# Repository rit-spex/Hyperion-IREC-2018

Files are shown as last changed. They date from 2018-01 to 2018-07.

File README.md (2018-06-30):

# IREC-Hyperion

###### Overview
Every year Spaceport America host the Intercollegiate Rocket and Engineering Competition or IREC. Teams for colleges from across the country meet to compete in these events. The 2018 SA Cup will be held June 19-23, 2018, with events held in Las Cruces, NM. RIT SPEX will be partnering with RIT Launch Initiative to deliver our first entry into the competition. Launch Initiative will build the rocket, SPEX will provide the payload. Our goal is to design and build a scientific payload to compete in the intercollegiate rocket engineering competition.

###### Repository Contents

* ***/hardware*** - Hardware design documents
* ***/IREC-Hyperion Documentation*** - Documentation files regarding the Hyperion project
* ***/IREC-Hyperion Drop Test*** - Files regarding drop tests
* ***/IREC-Hyperion HABnet Data Feeder*** - Ground station software which collects data transmitted from payload
* ***/IREC-Hyperion Protocol*** - The Hyperion protocol software library
* ***/IREC-Hyperion System*** - System source files and libraries for the Hyperion payload
* ***/IREC-Hyperion Tests*** - Hyperion test resources 

###### Mission Patch
Hyperion Mission Patch

###### Hardware Modules
- Teensy 3.6
- Sparkfun LIS331
- Sparkfun LSM9DS1
- Adafruit BME280
- Sparkfun CCS811
- RFM_9X LoRa
- PerfectFlite StratoLogger CF

###### Contributors

Daniel Mitchell

Alec Herbert

Thomas James Hall

Dylan R. Wagner

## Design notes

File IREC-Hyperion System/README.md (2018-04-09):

# IREC-Hyperion System

###### Summary 
This sub-directory contains libraries, source files and tests pertaining to the Hyperion System Software. The system software uses a handfull of Arduino libraries as-well as custom libraries. All source files are written in C/C++ with some test files written in The Arduino programming language (.ino). 

######  Contents
* ***/lib*** - Collection of Libraries used within the system
* ***/src*** - Source files for the Hyperion system
* ***/test*** - Collection of tests

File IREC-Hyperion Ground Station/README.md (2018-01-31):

# IREC-Hyperion HABnet Data Feeder
...

## Data Processor
Software running on ground base server.

...

### Dependencies 

## System Forwarder
Software running on Arduino micro controller.

...

### Dependencies

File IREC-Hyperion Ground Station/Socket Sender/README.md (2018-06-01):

## Hyperion Socket Sender
### Reads incoming data from a serial device (see:[System Forwarder](../System%20Forwarder)) and sends it to a [HABnet](https://github.com/RIT-Space-Exploration/HABnet) instance

--- 

**Requirements:**

* socketIO-client  ([github](https://github.com/invisibleroads/socketIO-client))

        pip install socketIO-client

* pyserial ([github](https://github.com/pyserial/pyserial))

        pip install pyserial

---

**Optional Arguments:**

* `-h`, `--help`

  show help message and exit

* `-D`, `--details`

  Display various details and close

* `-H [HOSTNAME]`, `--host [HOSTNAME]`

  HABnet instance hostname

  default: `127.0.0.1`

* `-P [PORT]`, `--port [PORT]`

  HABnet instance port

  default: `3000`

* `-S [SERIAL_IN]`, `--serial [SERIAL_IN]`

  Serial input port

  default: `COM3`

* `-N` [NAME], `--name [NAME]`

  HABnet socket name

  default: `testSocket`

---

**Examples:**

    python socketsender.py 
    python socketsender.py --host 127.0.0.1 --port 3000

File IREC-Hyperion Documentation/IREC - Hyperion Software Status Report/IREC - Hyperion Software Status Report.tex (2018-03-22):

\title{IREC - Hyperion Software Status Report}
\author{
	Dylan Wagner (drw6528@rit.edu) \\
	RIT Space Exploration
}

\date{\today}

\documentclass[11pt]{article}
\usepackage{hyperref} 
\hypersetup{
    colorlinks=true,
    linkcolor=blue,
    filecolor=magenta,      
    urlcolor=cyan,
}
\urlstyle{same}

\begin{document}
\maketitle

\section{Work Completed}
This section will outline work completed on the system software of the Hyperion payload. 
\begin{itemize}
  \item Inital testing of hardware modules:
  \begin{itemize}
  	\item LSM9DS1 (Accelerometer , Gyroscope, Magnetometer) Sensor
	\item BME280 (Pressure, Humidity, Temperature) Sensor
	\item CCS811 (TVOC, CO2) Sensor
	\item LIS331 (Accelerometer) Sensor
	\item RFM\_9X LoRa 
  \end{itemize}
  \item Utility functions for hardware modules
  \begin{itemize}
   	\item LSM9DS1 (Accelerometer , Gyroscope, Magnetometer) Sensor
	\item BME280 (Pressure, Humidity, Temperature) Sensor
	\item CCS811 (TVOC, CO2) Sensor
	\item LIS331 (Accelerometer) Sensor
	\item RFM\_9X LoRa 
  \end{itemize}
  \item Defining a communication protocol for the Hyperion Payload
  \item Implementing the payload communication protocol
  \item Creation of a robust execution scheduling queue (\href{https://github.com/RIT-Space-Exploration/Dynamic-Scheduling-Queue}{Dynamic Scheduling Queue})
  \item Forked RadioHead library to work with Teensy3.6
  \item Tested:
  \begin{itemize}
  	\item Communication between RFM\_9X modules 
	\item Communication between RFM\_9X modules using the Hyperion payload Protocol
	\item The Dynamic Scheduling Queue
	\item Communication routines within the the system
  \end{itemize}	
\end{itemize}

\section{In Progress / ToDo}
This section will outline work that is in progress or will be in the near future. 
\begin{itemize}
	\item Further defining routines within the system
	\item Implementation of routines regarding:
	\begin{itemize}
		\item Gathering data from sensors, logging it
		\item Transmission of data groups with the Hyperion Protocol
		\item Writing the data buffer to the storage card
		\item Mission Events (Parachute deployment, Impact damper deployment)
		\item Maintaining impact damper pressure
	\end{itemize}
	\item Testing implemented routines
	\item Initial testing of the Pressure Transducer 
	\item Utility functions for the Pressure Transducer 
	\item Further optimizing the Hyperion Protocol for low-bandwidth environments
	\item Testing deployment sensing mechanism 
	\item Testing software with mission event tests (Parachute deployment, Impact damper deployment)
	\item Readjustment of static priority values within the Dynamic Scheduling Queue.
	\item Testing of overall system
	\item Data feeder software for ground station:
	\begin{itemize}
		\item Software to collect transmissions from payload on a micro-controller 
		\item Software to collect data over serial from connected micro-controller and feed data to HabNet
	\end{itemize}
\end{itemize}

\section{Links}
\begin{itemize}
	\item The Rochester Institute of Technology Space Exploration Website
	\\ \url{http://spex.rit.edu}
	\item The Rochester Institute of Technology Space Exploration GitHub Page \url{https://github.com/RIT-Space-Exploration}
	\item IREC - Hyperion Main Repository (GitHub)
	\\ \url{https://github.com/RIT-Space-Exploration/IREC-Hyperion}
	\item Dynamic Scheduling Queue (GitHub)
	\\ \url{https://github.com/RIT-Space-Exploration/Dynamic-Scheduling-Queue}
	\item Forked RadioHead Library (GitHub)
	\\ \url{https://github.com/RIT-Space-Exploration/RadioHead}
\end{itemize}

\end{document}

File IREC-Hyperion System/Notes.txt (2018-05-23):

Notes
04/24/18
    Data Transmission Has been axed for the test launch.
        SPI bus conflict causes race condition which eventually causes LoRa module to hang.
05/17/18
    Move LIS331 and LSM9DS1 back to SPI0 - Done
05/20/18
    Implement routine which runs in safe phase and reports health of hardware.
        - Deployment Pins
        - EMatches 
        - SD card
        - Pressure system
        - Servo
        ...

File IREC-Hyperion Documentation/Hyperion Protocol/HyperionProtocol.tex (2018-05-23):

\documentclass{article}

\usepackage[table,xcdraw]{xcolor}
\usepackage{float}
\usepackage{fancyhdr}
\pagestyle{fancy}

\title{RIT SPEX Hyperion Protocol}
\date{February 1, 2018}
\author{Dylan R. Wagner, Alec Herbert, Chris Johnson}

\begin{document}
  \pagenumbering{gobble}
  \maketitle
  \pagenumbering{arabic}
  
  \section{Abstract}
  The Hyperion Protocol defines data packing techniques and configurations in order to achieve communication between endpoints. A universal header will be defined which allows senders the freedom to include a wide range of information from individual sensors or information groups. In addition, multiple other data configurations will be defined. These additional data configurations will store information regarding data groups from sensors without any notion of time captured.
  
  \section{Header}
  The header will be required for any outgoing and incoming data within the realm of the Hyperion protocol. This header will include information regarding the which data group (Sensor values) is contained in a message, flags and time sent. Any data wished to be sent with the Hyperion Protocol will be tacked on behind the header.  The Hyperion Protocol header will be \textbf{24bits} long or \textbf{3 bytes}.
  \subsection{Header Data}
  Data contained in the header will have a maximum size, this size will be defined in bits and largest value stored. 
  
  \paragraph{Data Group (4 bits)}
  The Data Group section will contain information to distinguish which data is contained after the header. A size of 4 bits will be allocated to this section, this allows for 16 separate values. This will be plenty for the number of data groups sent within the Hyperion system. 
  
  \paragraph{Flags (4 bits)}
  The Flags section will be used to define how the data will be parsed or handled. A size of 4 bits will allow for 4 flags to be set at a time.
  
  \paragraph{Sent Time (16 bits)}
  The Sent Time section will be used to determine the time sent in seconds from the Hyperion system. This will be used for timestamps/data evolution analysis. This section will need to be 16 bits. This allows for a value of maximum value of 65535. This allows us to send data time stamped from startup for 18.2 hours. 
  
  \subsection{Visualization}
  
  \begin{table}[h]
  \centering
  \caption{Hyperion Header}
  \label{Hyperion Header}
  \begin{tabular}{|c|c|c|l|l|l|l|l|l|l|lll}
  \cline{1-10}
  1 & 2 & \multicolumn{8}{c|}{Sent Time (16 bits)} &  & 1 & Data Group (4 bits) \\ \cline{1-10}
  \multicolumn{10}{|c|}{Data}                      &  & 2 & Flags (4 bits)      \\ \cline{1-10}
  \end{tabular}
  \end{table}
  
  \subsection{Header Values}
  This section displays mappings between header values and their meanings. In the header only two sections will need further definitions. These sections are the Data Group and Flags sections.
  
  \subsubsection{Data Group Mapping}
  
  \begin{table}[h]
  \centering
  \caption{Data Group Mapping}
  \begin{tabular}{ll}
  Value & Mapping \\
  0     & No Data \\
  1     & LSM9DS1     \\
  2     & BME280        \\
  3     & CCS811        \\
  4     & LIS331      \\
  5     & PerfectFlite Strato Logger       \\
  6     & Orientation   \\
  7     &  Commands  \\
  8     &         \\
  9     &         \\
  10    &         \\
  11    &         \\
  12    &         \\
  13    &         \\
  14    &         \\
  15    &        
  \end{tabular}
  \end{table}
  
  \pagebreak
  
  \section{Data Groups}
  \subsection{LSM9DS1}
  This section will define the data frame for the LSM9DS1 data group. The LSM9DS1 data group contains information regarding acceleration, gyroscope and magnetometer sensors in the X, Y and Z axis. In total, this data frame will be 36 bytes in size. 
  \subsubsection{LSM9DS1 Data}
  \paragraph{Acceleration X, Y, Z (12 bytes - 96 bits)}
  The acceleration section of the LSM9DS1 data frame will store the X, Y, Z values. Each axis is 4 bytes or 32 bits long. The X, Y, Z values will be placed in that order.
  \paragraph{Gyroscope X, Y, Z (12 bytes - 96 bits)}
  The gyroscope section of the LSM9DS1 data frame will store the X, Y, Z values. Each axis is 4 bytes or 32 bits long. The X, Y, Z values will be placed in that order.
  \paragraph{Magnetometer X, Y, Z (12 bytes - 96 bits)}
  The magnetometer section of the LSM9DS1 data frame will store the X, Y, Z values. Each axis is 4 bytes or 32 bits long. The X, Y, Z values will be placed in that order.
  \subsubsection{Visualization}
  
  \begin{table}[h]
  \centering
  \caption{LSM9DS1 Data frame}
  \begin{tabular}{|l|l|l|l|l|l|l|l|l|l|l|l|}
  \hline
  \multicolumn{4}{|l|}{ax (4 bytes)} & \multicolumn{4}{l|}{ay (4 bytes)} & \multicolumn{4}{l|}{az (4 bytes)} \\ \hline
  \multicolumn{4}{|l|}{gx (4 bytes)} & \multicolumn{4}{l|}{gy (4 bytes)} & \multicolumn{4}{l|}{gz (4 bytes)} \\ \hline
  \multicolumn{4}{|l|}{mx (4 bytes)} & \multicolumn{4}{l|}{my (4 bytes)} & \multicolumn{4}{l|}{mz (4 bytes)} \\ \hline
  \end{tabular}
  \end{table}

  \pagebreak

  \subsection{BME280}
  This section will define the data frame for the BME280 data group. The BME280 data group contains information regarding atmospheric temperature, pressure and humidity. In total, this data frame will be 8 bytes in size.
  \subsubsection{BME280 Data}
  \paragraph{Temperature (2 bytes)}
  The temperature section of the BME280 data frame will store the atmospheric temperature in degrees Celsius. In total, the temperature section will be 2 bytes.
  \paragraph{Pressure (2 bytes)}
  The pressure section of the BME280 data frame will store the atmospheric pressure in kPa. In total, the pressure section will be 2 bytes.
  \paragraph{Humidity (2 bytes)}
  The humidity section of the BME280 data frame will store the atmospheric humidity by percentage. In total, the humidity section will be 4 bytes.
  \paragraph{BME\_Altitude (2 bytes)}
  The Altitude section of the BME280 data frame will store the altitude derived by pressure. In total, the BME\_Altitude section will be 2 bytes.
  \subsubsection{Visualization}
  
  \begin{table}[H]
  \centering
  \caption{BME280 Data Group}
  \label{my-label}
  \begin{tabular}{|l|l|}
  \hline
Temperature (2 bytes) & Pressure (2 bytes)      \\ \hline
Humidity (2 bytes)    & BME\_Altitude (2 bytes) \\ \hline
  \end{tabular}
  \end{table}
  
  \pagebreak
  
  \subsection{CCS811}
  This section will define the data frame for the the CCS811 data group. The CCS811 data group contains information regarding atmospheric composition. In,      total, this data frame will be 4 bytes in size.
  \subsubsection{CCS811 Data}
  \paragraph{Total Volatile Organic Compounds (2 Bytes)}
  The Total Volatile Organic Compounds section of the CCS811 data frame will store the total volatile organic compounds in ppm. In total, this section will be 2 bytes.
  \paragraph{Equivalent Carbon Dioxide (2 Bytes)}
  The Equivalent Carbon Dioxide section of the CCS811 data frame will store the equivalent carbon dioxide in ppm. In total, this section will be 2 bytes in size.
  \subsubsection{Visualization}
  
  \begin{table}[H]
  \centering
  \caption{CCS811 Data Frame}
  \label{my-label}
  \begin{tabular}{|l|l|}
  \hline
VOC (2 bytes) & ECD (2 bytes) \\ \hline 
  \end{tabular}
  \end{table}
 
  \pagebreak
 
 \subsection{LIS331}
 This section will define the data frame for the the LIS331 data group. The LIS331 data group contains information acceleration in Gees. In,  total, this data frame will be 12 bytes in size.
 \subsubsection{LIS331 Data}
 \paragraph{X, Y, Z Acceleration (12 bytes)}
 The Acceleration section of the LIS331 data frame will store the acceleration sensor readings in Gees. The X, Y, Z parts of this section will be 4 bytes each. In total, this data section will be 12 bytes.
 \subsubsection{Visualization}
 
 \begin{table}[H]
 \centering
 \caption{LIS331 Data Frame}
 \label{my-label}
 \begin{tabular}{|l|l|l|}
 \hline
Acceleration (X) & Acceleration (Y) & Acceleration (Z) \\ \hline
 \end{tabular}
 \end{table}
 
 \pagebreak
 
  \subsection{PerfectFlite Strato Logger}
  This section will define the data frame for the Strato Logger data group. The Strato Logger data group provides accurate information regarding altitude. In total, this data group will be 4 bytes in size.
  \subsubsection{Strato Logger Data}
  \paragraph{Altitude (4 bytes)}
  The Altitude section of the Strato Logger data group will store the altitude in meters. In total, this data section will be 4 bytes in size.
  
  \subsubsection{Visualization}
  \begin{table}[H]
  \centering
  \caption{PerfectFlite Strato Logger Data Group}
  \label{my-label}
  \begin{tabular}{|l|}
  \hline
Altitude (2 bytes) \\ \hline
 \end{tabular}
 \end{table}
  
 \pagebreak
  
  \subsection{Orientation}
  
  This section will define the data frame for the Orientation data group. The Orientation data group will contain calculations for Roll, Pitch and Yaw. In total, this data group will be 4 bytes in size. Values will be 9 bits in length with the signed bits being stored within the first byte. 
  \subsubsection{Orientation Data}
  \paragraph{Roll (9 bits)}
  The Roll section of the Orientation data group will store the Roll from range -180 to 180 (0 to 360 degrees).
  \paragraph{Pitch (9 bits)}
  The Pitch section of the Orientation data group will store the Pitch from range -90 to 90 (0 to 180 degrees).  
  \paragraph{Yaw (9 bits)}
  The Yaw section of the Orientation data group will store the Yaw from range -180 to 180 (0 to 360 degrees).  
  
  \subsubsection{Visualization}
  \begin{table}[H]
  \centering
  \caption{Orientation Data Group}
  \label{Orientation}
  \begin{tabular}{|l|l|l|l|}
  \hline
  
Signed(1 byte) & Roll(1 byte) & Pitch(1 byte) & Yaw(1 byte) \\ \hline

  \end{tabular}
  \end{table}
  
 \pagebreak  
  
  \subsection{Commands/Command Info}
  This section will outline the header configurations for separate commands to and from the payload. This Group will hold no data, thus this data frame is 0 bytes in size. Header flags will be used in place of a data frame.
  \subsubsection{Flags}

  \begin{table}[h]
  \centering
  \caption{Flag Meanings}
  \begin{tabular}{ll}
    Bit Pos(Most significant) & Meaning \\
  0     & Arm Payload \\
  1     & Disarm Payload     \\
  2     & Payload Armed        \\
  3     & Payload Disarmed       \\
  \end{tabular}
  \end{table}
  
  \pagebreak
  
  \subsection{Info Messages}
  This section will outline the anatomy of a info message data frame. This data frame has no defined length, only a length of greater than 3 bytes.
  
  \subsubsection{Data}
  Data attached to this frame will be stored in the form of a string. This string has no defined length. However it will be less than the maximum length of transmitted packets defined by the communication device.
   
  \lfoot{Latest Revision: \today}

  \end{document}

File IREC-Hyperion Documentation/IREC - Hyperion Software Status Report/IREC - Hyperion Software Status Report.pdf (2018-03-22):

## IREC - Hyperion Software Status Report

Dylan Wagner (drw6528@rit.edu) RIT Space Exploration

March 22, 2018

## 1 Work Completed

This section will outline work completed on the system software of the Hyperion payload.

- Inital testing of hardware modules:

– LSM9DS1 (Accelerometer , Gyroscope, Magnetometer) Sensor

– BME280 (Pressure, Humidity, Temperature) Sensor

– CCS811 (TVOC, CO2) Sensor

– LIS331 (Accelerometer) Sensor

– RFM 9X LoRa

- Utility functions for hardware modules

– LSM9DS1 (Accelerometer , Gyroscope, Magnetometer) Sensor

– BME280 (Pressure, Humidity, Temperature) Sensor

– CCS811 (TVOC, CO2) Sensor

– LIS331 (Accelerometer) Sensor

– RFM 9X LoRa

- Defining a communication protocol for the Hyperion Payload
- Implementing the payload communication protocol
- Creation of a robust execution scheduling queue (Dynamic Scheduling Queue) (https://github.com/RIT-Space-Exploration/Dynamic-Scheduling-Queue)
- Forked RadioHead library to work with Teensy3.6

1

- Tested:

– Communication between RFM 9X modules

– Communication between RFM 9X modules using the Hyperion payload Protocol

– The Dynamic Scheduling Queue

– Communication routines within the the system

## 2 In Progress / ToDo

This section will outline work that is in progress or will be in the near future.

- Further defining routines within the system
- Implementation of routines regarding:

– Gathering data from sensors, logging it

– Transmission of data groups with the Hyperion Protocol

– Writing the data buffer to the storage card

– Mission Events (Parachute deployment, Impact damper deployment)

– Maintaining impact damper pressure

- Testing implemented routines
- Initial testing of the Pressure Transducer
- Utility functions for the Pressure Transducer
- Further optimizing the Hyperion Protocol for low-bandwidth environments
- Testing deployment sensing mechanism
- Testing software with mission event tests (Parachute deployment, Impact damper deployment)
- Readjustment of static priority values within the Dynamic Scheduling Queue.
- Testing of overall system

2

- Data feeder software for ground station:

– Software to collect transmissions from payload on a micro-controller

– Software to collect data over serial from connected micro-controller and feed data to HabNet

## 3 Links

- The Rochester Institute of Technology Space Exploration Website http://spex.rit.edu
- The Rochester Institute of Technology Space Exploration GitHub Page https://github.com/RIT-Space-Exploration
- IREC - Hyperion Main Repository (GitHub) https://github.com/RIT-Space-Exploration/IREC-Hyperion
- Dynamic Scheduling Queue (GitHub) https://github.com/RIT-Space-Exploration/Dynamic-Scheduling-Queue
- Forked RadioHead Library (GitHub) https://github.com/RIT-Space-Exploration/RadioHead

3

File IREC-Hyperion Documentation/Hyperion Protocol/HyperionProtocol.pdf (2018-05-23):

# RIT SPEX Hyperion Protocol

Dylan R. Wagner, Alec Herbert, Chris Johnson

February 1, 2018

## 1 Abstract

The Hyperion Protocol defines data packing techniques and configurations in order to achieve communication between endpoints. A universal header will be defined which allows senders the freedom to include a wide range of information from individual sensors or information groups. In addition, multiple other data configurations will be defined. These additional data configurations will store information regarding data groups from sensors without any notion of time captured.

## 2 Header

The header will be required for any outgoing and incoming data within the realm of the Hyperion protocol. This header will include information regarding the which data group (Sensor values) is contained in a message, flags and time sent. Any data wished to be sent with the Hyperion Protocol will be tacked on behind the header. The Hyperion Protocol header will be 24bits long or 3 bytes.

### 2.1 Header Data

Data contained in the header will have a maximum size, this size will be defined in bits and largest value stored.

Data Group (4 bits) The Data Group section will contain information to distinguish which data is contained after the header. A size of 4 bits will be allocated to this section, this allows for 16 separate values. This will be plenty for the number of data groups sent within the Hyperion system.

Flags (4 bits) The Flags section will be used to define how the data will be parsed or handled. A size of 4 bits will allow for 4 flags to be set at a time.

1

2.2 Visualization | 2 HEADER

Sent Time (16 bits) The Sent Time section will be used to determine the time sent in seconds from the Hyperion system. This will be used for times-tamps/data evolution analysis. This section will need to be 16 bits. This allows for a value of maximum value of 65535. This allows us to send data time stamped from startup for 18.2 hours.

### 2.2 Visualization

Table 1: Hyperion Header
1 | 2 | Sent Time (16 bits) | 1 | Data Group (4 bits)
| | Data | 2 | Flags (4 bits)

### 2.3 Header Values

This section displays mappings between header values and their meanings. In the header only two sections will need further definitions. These sections are the Data Group and Flags sections.

### 2.3.1 Data Group Mapping

Table 2: Data Group Mapping
Value | Mapping
0 | No Data
1 | LSM9DS1
2 | BME280
3 | CCS811
4 | LIS331
5 | PerfectFlite Strato Logger
6 | Orientation
7 | Commands
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
3 DATA GROUPS

## 3 Data Groups

### 3.1 LSM9DS1

This section will define the data frame for the LSM9DS1 data group. The LSM9DS1 data group contains information regarding acceleration, gyroscope and magnetometer sensors in the X, Y and Z axis. In total, this data frame will be 36 bytes in size.

### 3.1.1 LSM9DS1 Data

Acceleration X, Y, Z (12 bytes - 96 bits) The acceleration section of the LSM9DS1 data frame will store the X, Y, Z values. Each axis is 4 bytes or 32 bits long. The X, Y, Z values will be placed in that order.

Gyroscope X, Y, Z (12 bytes - 96 bits) The gyroscope section of the LSM9DS1 data frame will store the X, Y, Z values. Each axis is 4 bytes or 32 bits long. The X, Y, Z values will be placed in that order.

Magnetometer X, Y, Z (12 bytes - 96 bits) The magnetometer section of the LSM9DS1 data frame will store the X, Y, Z values. Each axis is 4 bytes or 32 bits long. The X, Y, Z values will be placed in that order.

### 3.1.2 Visualization

Table 3: LSM9DS1 Data frame
ax (4 bytes) | ay (4 bytes) | az (4 bytes)
gx (4 bytes) | gy (4 bytes) | gz (4 bytes)
mx (4 bytes) | my (4 bytes) | mz (4 bytes)

3

3.2 BME280 | 3 DATA GROUPS

### 3.2 BME280

This section will define the data frame for the BME280 data group. The BME280 data group contains information regarding atmospheric temperature, pressure and humidity. In total, this data frame will be 8 bytes in size.

### 3.2.1 BME280 Data

Temperature (2 bytes) The temperature section of the BME280 data frame will store the atmospheric temperature in degrees Celsius. In total, the temperature section will be 2 bytes.

Pressure (2 bytes) The pressure section of the BME280 data frame will store the atmospheric pressure in kPa. In total, the pressure section will be 2 bytes.

Humidity (2 bytes) The humidity section of the BME280 data frame will store the atmospheric humidity by percentage. In total, the humidity section will be 4 bytes.

BME Altitude (2 bytes) The Altitude section of the BME280 data frame will store the altitude derived by pressure. In total, the BME Altitude section will be 2 bytes.

### 3.2.2 Visualization

Table 4: BME280 Data Group
Temperature (2 bytes) | Pressure (2 bytes)
Humidity (2 bytes) | BME Altitude (2 bytes)

4

3.3 CCS811 | 3 DATA GROUPS

### 3.3 CCS811

This section will define the data frame for the the CCS811 data group. The CCS811 data group contains information regarding atmospheric composition. In, total, this data frame will be 4 bytes in size.

### 3.3.1 CCS811 Data

Total Volatile Organic Compounds (2 Bytes) The Total Volatile Organic Compounds section of the CCS811 data frame will store the total volatile organic compounds in ppm. In total, this section will be 2 bytes.

Equivalent Carbon Dioxide (2 Bytes) The Equivalent Carbon Dioxide section of the CCS811 data frame will store the equivalent carbon dioxide in ppm. In total, this section will be 2 bytes in size.

### 3.3.2 Visualization

Table 5: CCS811 Data Frame VOC (2 bytes) ECD (2 bytes)

5

3.4 LIS331 | 3 DATA GROUPS

### 3.4 LIS331

This section will define the data frame for the the LIS331 data group. The LIS331 data group contains information acceleration in Gees. In, total, this data frame will be 12 bytes in size.

### 3.4.1 LIS331 Data

X, Y, Z Acceleration (12 bytes) The Acceleration section of the LIS331 data frame will store the acceleration sensor readings in Gees. The X, Y, Z parts of this section will be 4 bytes each. In total, this data section will be 12 bytes.

### 3.4.2 Visualization

Table 6: LIS331 Data Frame
Acceleration (X) | Acceleration (Y) | Acceleration (Z)

6

3.5 PerfectFlite Strato Logger | 3 DATA GROUPS

### 3.5 PerfectFlite Strato Logger

This section will define the data frame for the Strato Logger data group. The Strato Logger data group provides accurate information regarding altitude. In total, this data group will be 4 bytes in size.

### 3.5.1 Strato Logger Data

Altitude (4 bytes) The Altitude section of the Strato Logger data group will store the altitude in meters. In total, this data section will be 4 bytes in size.

### 3.5.2 Visualization

Table 7: PerfectFlite Strato Logger Data Group Altitude (2 bytes)

7

3.6 Orientation | 3 DATA GROUPS

### 3.6 Orientation

This section will define the data frame for the Orientation data group. The Orientation data group will contain calculations for Roll, Pitch and Yaw. In total, this data group will be 4 bytes in size. Values will be 9 bits in length with the signed bits being stored within the first byte.

### 3.6.1 Orientation Data

Roll (9 bits) The Roll section of the Orientation data group will store the Roll from range -180 to 180 (0 to 360 degrees).

Pitch (9 bits) The Pitch section of the Orientation data group will store the Pitch from range -90 to 90 (0 to 180 degrees).

Yaw (9 bits) The Yaw section of the Orientation data group will store the Yaw from range -180 to 180 (0 to 360 degrees).

### 3.6.2 Visualization

Table 8: Orientation Data Group
Signed(1 byte) | Roll(1 byte) | Pitch(1 byte) | Yaw(1 byte)

8

3.7 Commands/Command Info | 3 DATA GROUPS

### 3.7 Commands/Command Info

This section will outline the header configurations for separate commands to and from the payload. This Group will hold no data, thus this data frame is 0 bytes in size. Header flags will be used in place of a data frame.

### 3.7.1 Flags

Table 9: Flag Meanings
Bit Pos(Most significant) | Meaning
0 | Arm Payload
1 | Disarm Payload
2 | Payload Armed
3 | Payload Disarmed

9

3.8 Info Messages | 3 DATA GROUPS

### 3.8 Info Messages

This section will outline the anatomy of a info message data frame. This data frame has no defined length, only a length of greater than 3 bytes.

### 3.8.1 Data

Data attached to this frame will be stored in the form of a string. This string has no defined length. However it will be less than the maximum length of transmitted packets defined by the communication device.

Latest Revision: May 19, 2018 | 10

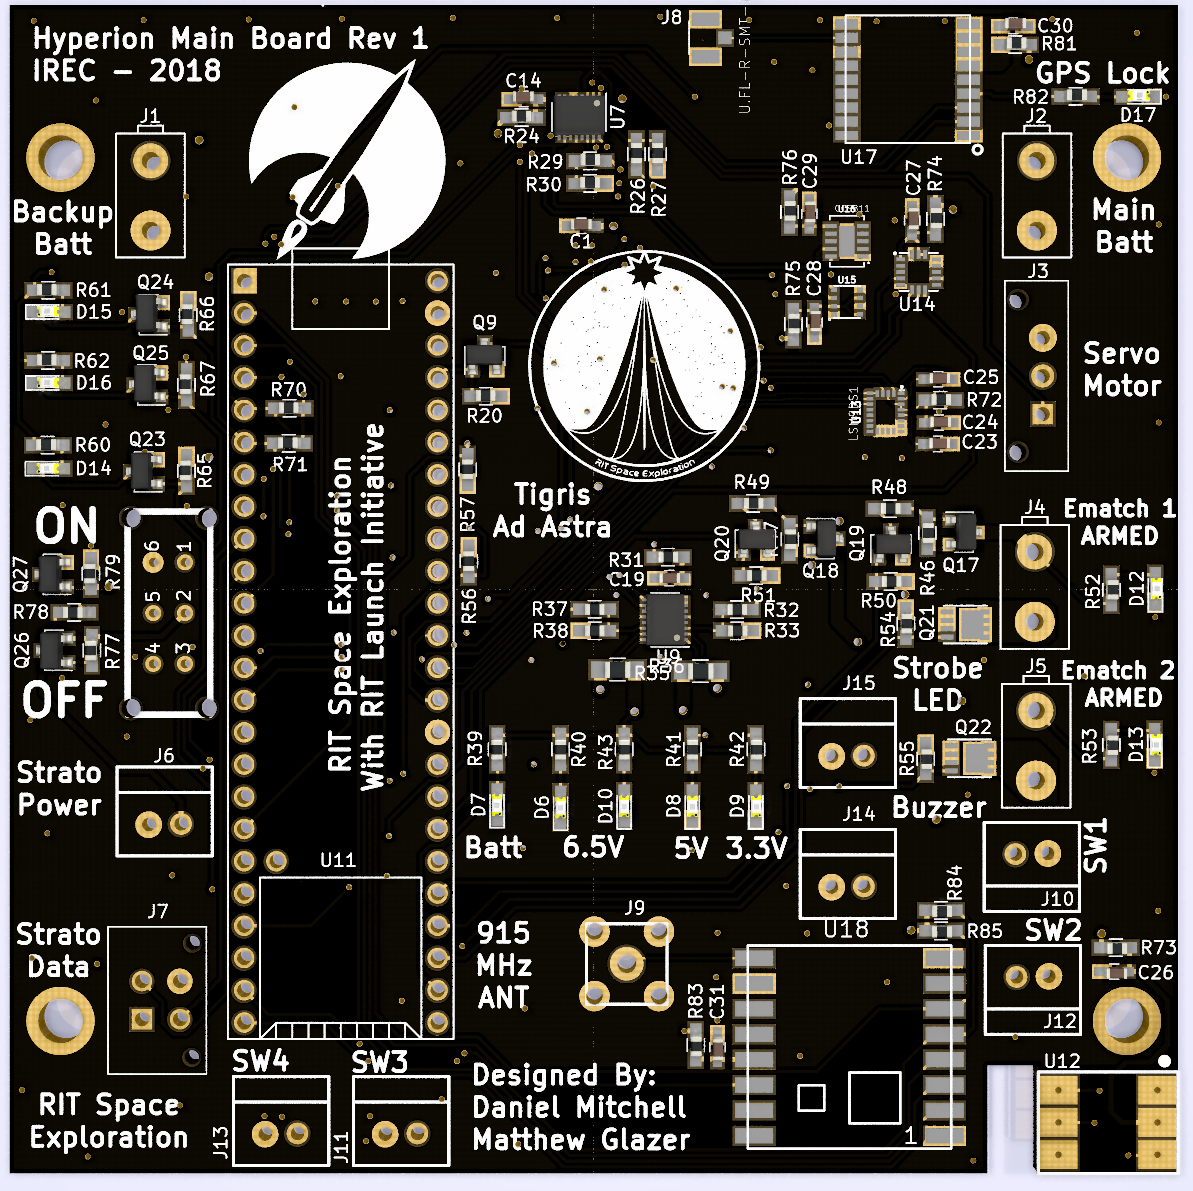
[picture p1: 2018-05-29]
Hardware/MainboardRev1/Images/Front_Rev1.PNG

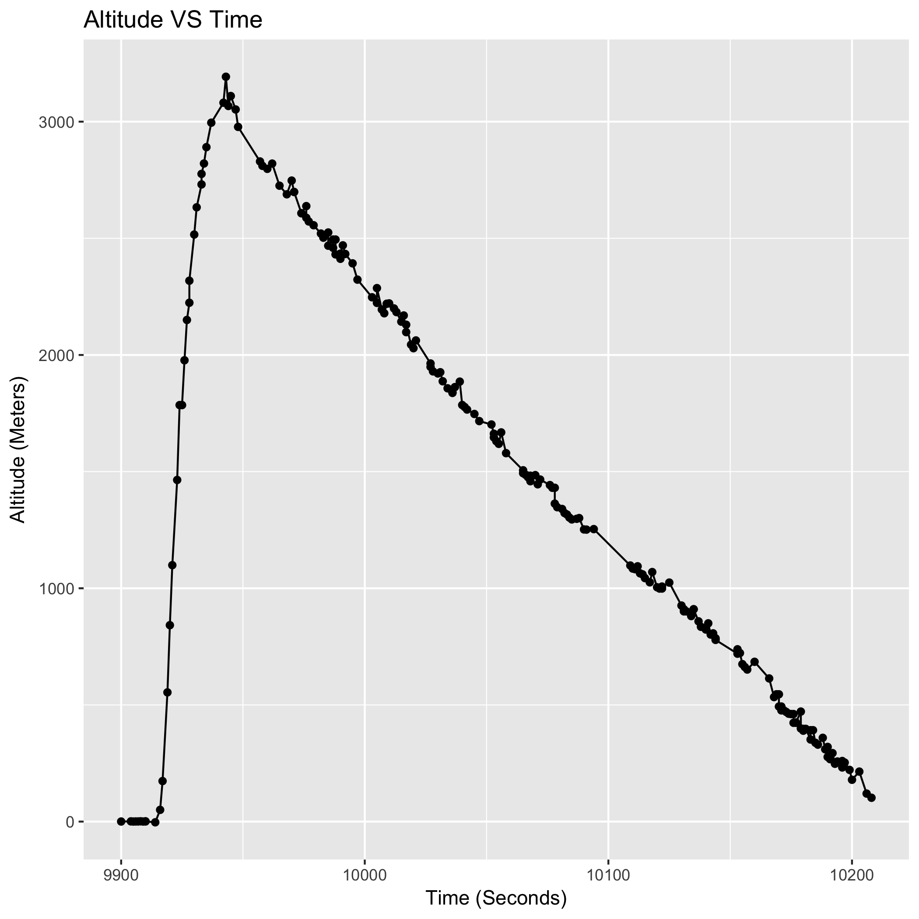
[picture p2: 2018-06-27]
IREC 2018 Flight/Scripts/alt.png

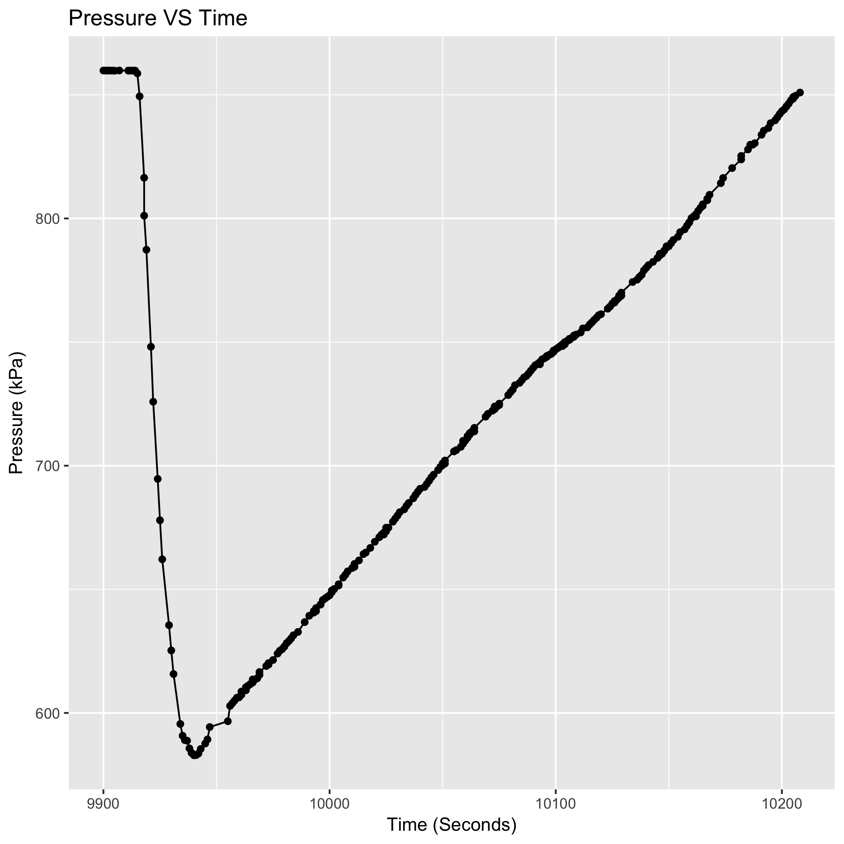
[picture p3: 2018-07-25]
IREC 2018 Flight/Scripts/Pressure.png

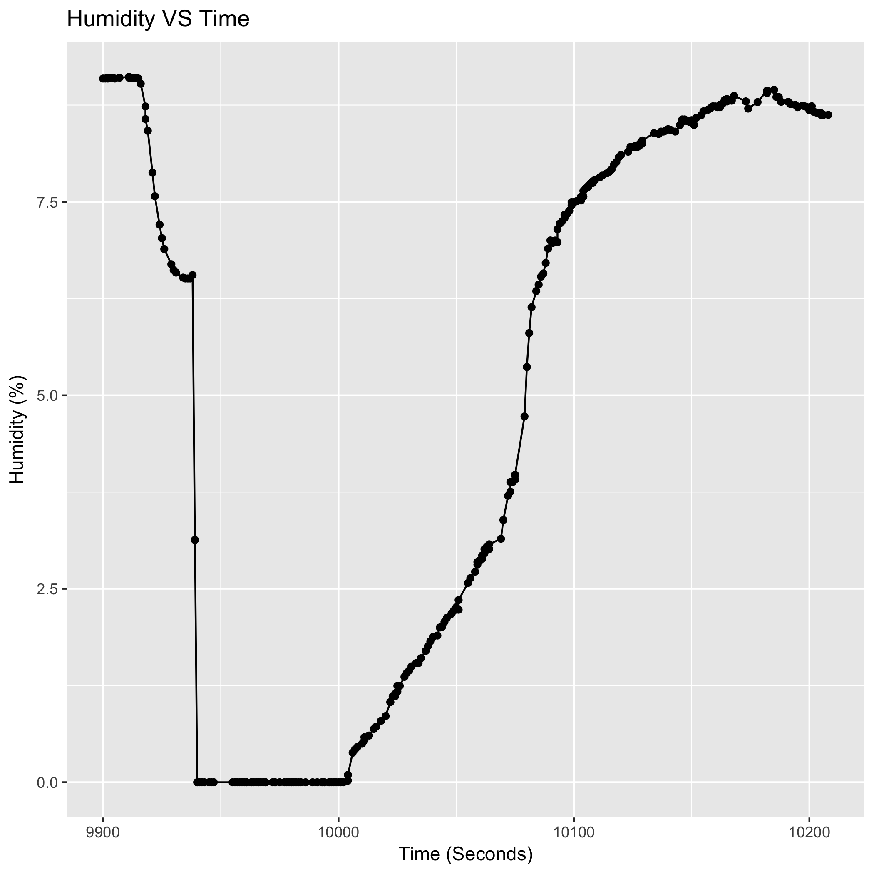
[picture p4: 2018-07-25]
IREC 2018 Flight/Scripts/Humidity.png

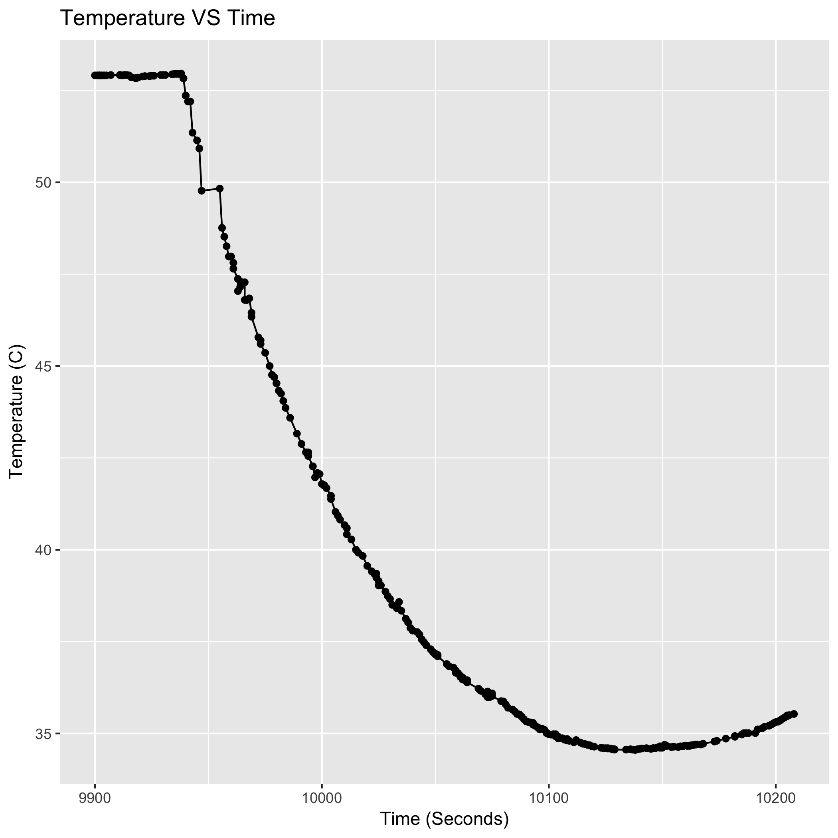
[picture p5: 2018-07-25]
IREC 2018 Flight/Scripts/Temperature.png

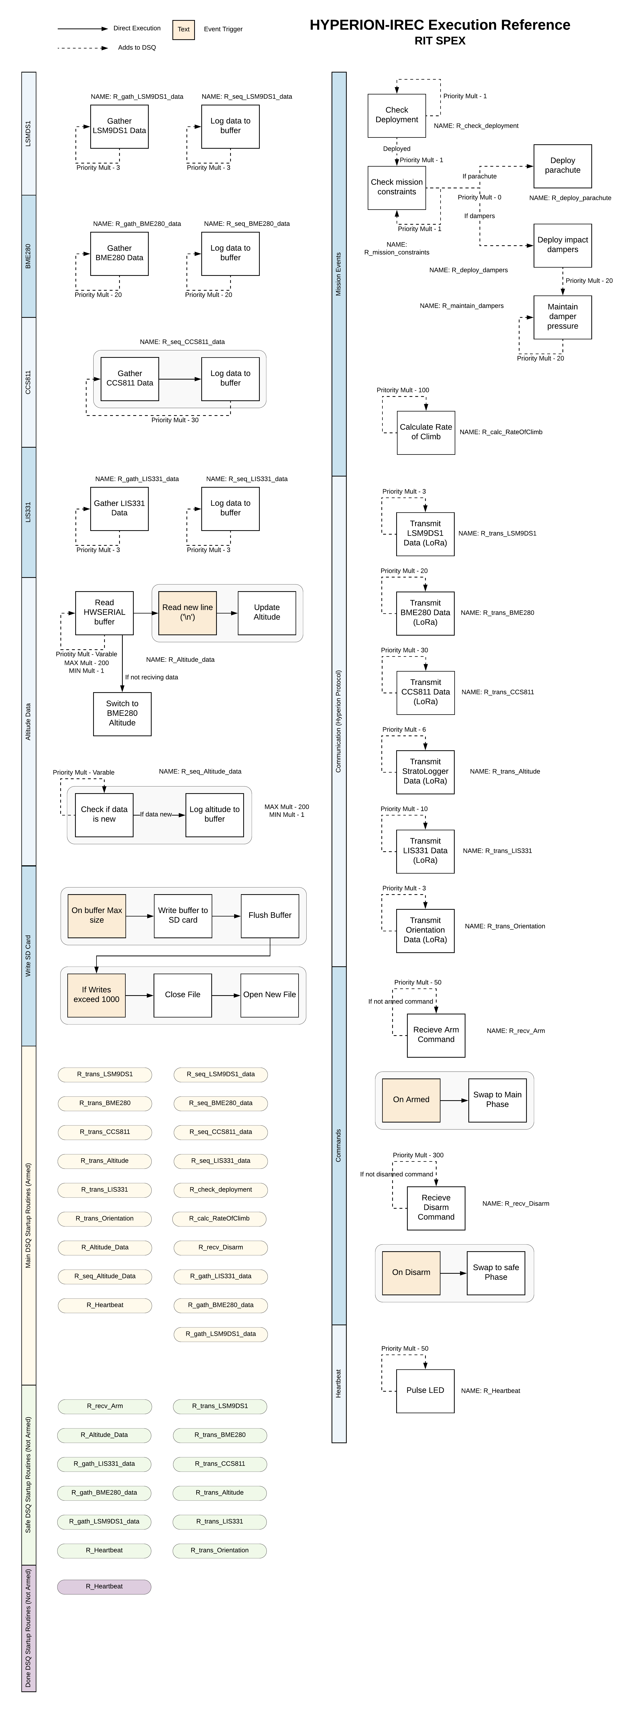
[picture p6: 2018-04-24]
IREC-Hyperion Documentation/Hyperion-IREC Execution Reference/HYPERION-IREC Execution Reference.png

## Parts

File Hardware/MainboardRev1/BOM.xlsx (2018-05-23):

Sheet: Rev 1
RIT Space Exploration - Hyperion Scientific Payload for the Intercollegiate Rocket Engineering Competition Main board Rev 1 Bill of Materials
Ref | Description | Manf Part Number | Manf | Footprint | Purchase Link | Quantity | Price | Sub Total
C4 C23 C32 C33 C34 C35 | .01uF, 100V |  |  | 0603 | Digikey (https://www.digikey.com/product-detail/en/tdk-corporation/C1608X7R2A103M080AA/445-1305-1-ND/567707)
C1 C5 C6 C14 C19 C24 C25 C26 C27 C28 C29 C30 C31 | 0.1uF, 50V |  |  | 0603 | Digikey (https://www.digikey.com/product-detail/en/samsung-electro-mechanics/CL10B104MB8NNNC/1276-1941-1-ND/3890027)
C7 | 10pF, 25V |  |  | 0603 | Digikey (https://www.digikey.com/product-detail/en/avx-corporation/06033C100KAT2A/478-11366-1-ND/8019119)
C8 | 220pF, 100V |  |  | 0603 | Digikey (https://www.digikey.com/product-detail/en/samsung-electro-mechanics/CL10B221KC8WPNC/1276-6656-1-ND/5961515)
C2 C3 C9 C10 C11 C12 C13 C15 C16 C17 C18 C20 C21 C22 | 47uF, 16V |  |  | 1210 | Digikey (https://www.digikey.com/product-detail/en/murata-electronics-north-america/GRM32ER61C476ME15K/490-8355-1-ND/4380649)
D5 | 3.3V Zener |  |  |  | Digikey (https://www.digikey.com/product-detail/en/vishay-semiconductor-diodes-division/BZX384B5V6-E3-18/BZX384B5V6-E3-18GICT-ND/8564886)
D1 D2 | 5.6V Zener |  |  |  | Digikey (https://www.digikey.com/product-detail/en/diodes-incorporated/MMSZ5232BS-7-F/MMSZ5232BS-FDICT-ND/815868)
D3 | Schottky Diode (Switching Regulator) |  |  |  | Digikey (https://www.digikey.com/product-detail/en/central-semiconductor-corp/CMDSH2-3-TR/CMDSH2-3CT-ND/4806979)
D15 D17 | Blue LED | 3.3Vf, 20mA, 104mcd |  |  | Digikey (https://www.digikey.com/product-detail/en/lite-on-inc/LTST-C194TBKT/160-1837-1-ND/2356236)
D6 D7 D8 D9 D14 | Green LED | 3.4Vf, 10mA, 98mcd |  |  | Digikey (https://www.digikey.com/product-detail/en/osram-opto-semiconductors-inc/LT-L29S-P2R1-25-Z/475-2774-1-ND/1938941)
D10 D12 D13 D16 | Red LED | 2Vf, 20mA, 104mcd |  |  | Digikey (https://www.digikey.com/product-detail/en/osram-opto-semiconductors-inc/LS-Q976-NR-1/475-2512-1-ND/1802639)
D4 D11 | Schottky Diode 20V 4A |  |  |  | Digikey (https://www.digikey.com/product-detail/en/vishay-semiconductor-diodes-division/SL42-E3-57T/SL42-E3-57TGICT-ND/1091621)
J9 |  | CONN_RP-SMA_Right_Angle_0733910320 |  |  | Digikey (https://www.digikey.com/products/en?keywords=0733910320)
J1 J2 J4 J5 |  | CONN_2POS_VERT_TE_CONN |  |  | Digikey (https://www.digikey.com/scripts/DkSearch/dksus.dll?Detail&itemSeq=261636948&uq=636626302055901696)
Mates for Above |  |  |  |  | Digikey (https://www.digikey.com/scripts/DkSearch/dksus.dll?Detail&itemSeq=261636940&uq=636626302055891695)
J6 J10 J11 J12 J13 J14 J15 |  |  |  |  | Digikey (https://www.digikey.com/scripts/DkSearch/dksus.dll?Detail&itemSeq=261713276&uq=636626432256830487)
Mates for Above |  |  |  |  | Digikey (https://www.digikey.com/scripts/DkSearch/dksus.dll?Detail&itemSeq=261713294&uq=636626432256830487)
J3 |  | Molex_Microfit3_Header_01x03_Straight |  |  | Digikey (https://www.digikey.com/product-detail/en/molex-llc/0436500315/WM1918-ND/283462)
Mates for Above |  |  |  |  | Digikey (https://www.digikey.com/product-detail/en/molex-llc/43645-0300/WM1846-ND/268975)
J7 |  | 4-Pin_Molex_Vertical |  |  | Digikey (https://www.digikey.com/product-detail/en/molex-llc/0430450427/WM10667-ND/3310189)
Mates for Above |  |  |  |  | Digikey (https://www.digikey.com/product-detail/en/molex-llc/0430250408/WM11225-ND/4481508)
J8 |  | HRS_U.FL-R-SMT-1(10) |  |  | Digikey (https://www.digikey.com/scripts/DkSearch/dksus.dll?Detail&itemSeq=261624801&uq=636626300194543747)
TE Connectivity AMP Pins |  |  |  |  | Digikey (https://www.digikey.com/scripts/DkSearch/dksus.dll?Detail&itemSeq=261705411&uq=636626302055951701)
Other TE Connectivity Pins??? |  |  |  |  | Digikey (https://www.digikey.com/scripts/DkSearch/dksus.dll?Detail&itemSeq=261713305&uq=636626432256840488)
Molex Pins |  |  |  |  | Digikey (https://www.digikey.com/product-detail/en/molex-llc/43030-0001/WM1837CT-ND/467810)
 |  |  |  |  |  | 0 |  | 0.00
L1 | 2.2uH | RLF7030T-2R2M5R4 |  |  | Digikey (https://www.digikey.com/product-detail/en/tdk-corporation/RLF7030T-2R2M5R4/445-2962-1-ND/1068729)
 |  |  |  |  |  | 0 |  | 0.00
Q5 Q6 Q7 Q9 Q11 Q12 Q13 Q14 Q16 Q19 Q20 Q23 Q24 Q25 Q27 Q30 Q31 |  | NTR4003 |  |  | Digikey (https://www.digikey.com/product-detail/en/on-semiconductor/NTR4003NT3G/NTR4003NT3GOSCT-ND/1967271)
Q21 Q22 |  | SIS612EDNT-T1-GE3 |  |  | Digikey (https://www.digikey.com/product-detail/en/vishay-siliconix/SIS612EDNT-T1-GE3/SIS612EDNT-T1-GE3CT-ND/7622753)
Q1 Q2 Q3 Q4 Q8 Q10 Q15 Q17 Q18 Q26 Q28 Q29 |  | SSM3J328R |  |  | Digikey (https://www.digikey.com/product-detail/en/toshiba-semiconductor-and-storage/SSM3J358RLF/SSM3J358RLFCT-ND/7394090)
 |  |  |  |  |  | 0 |  | 0.00
R80 | 0 | 0 |  |  | Digikey (https://www.digikey.com/product-detail/en/vishay-dale/CRCW06030000Z0EA/541-0.0GCT-ND/1179296)
R5 R24 R31 R72 R73 R74 R75 R76 R81 R83 | 10 | 10 |  |  | Digikey (https://www.digikey.com/product-detail/en/rohm-semiconductor/ESR03EZPJ100/RHM10DCT-ND/1983775)
R1 R2 R34 | 100k | 100k |  |  | Digikey (https://www.digikey.com/product-detail/en/rohm-semiconductor/ESR03EZPF1003/RHM100KADCT-ND/1983754)
R4 R6 R8 R12 R13 R16 R18 R20 R21 R23 R44 R45 R46 R47 R50 R51 R54 R55 R65 R66 R67 R70 R71 R77 R79 R84 R85 R86 R87 R90 R91 R94 R95 R98 R99 | 10k | 10k |  |  | Digikey (https://www.digikey.com/product-detail/en/vishay-dale/CRCW060310K0FKEA/541-10.0KHCT-ND/1179924)
R25 R28 | 10m | 10m |  |  | Digikey (https://www.digikey.com/product-detail/en/susumu/KRL1220E-M-R010-F-T5/408-1544-1-ND/3737726)
R59 R64 R69 | 11.3k | 11.3k |  |  | Digikey (https://www.digikey.com/product-detail/en/panasonic-electronic-components/ERJ-3EKF1132V/P11.3KHCT-ND/198121)
R27 R30 R33 R38 | 11.5k | 11.5k |  |  | Digikey (https://www.digikey.com/product-detail/en/yageo/RC0603FR-0711K5L/311-11.5KHRCT-ND/729848)
R17 | 118k | 118k |  |  | Digikey (https://www.digikey.com/product-detail/en/panasonic-electronic-components/ERJ-3EKF1183V/P118KHCT-ND/198134)
R10 R11 R22 R48 R49 R78 R96 R97 | 12k | 12k |  |  | Digikey (https://www.digikey.com/product-detail/en/yageo/RC0603FR-0712KL/311-12.0KHRCT-ND/729860)
R3 | 140k | 140k |  |  | Digikey (https://www.digikey.com/product-detail/en/yageo/RC0603FR-07140KL/311-140KHRCT-ND/729894)
R43 R62 | 150 | 150 |  |  | Digikey (https://www.digikey.com/product-detail/en/vishay-dale/CRCW0603150RFKEAHP/541-150SCT-ND/2825983)
R15 | 16k | 16k |  |  | Digikey (https://www.digikey.com/product-detail/en/rohm-semiconductor/KTR03EZPF1602/RHM16KAYCT-ND/4054109)
R26 R29 R32 R37 R56 R57 | 1M | 1M |  |  | Digikey (https://www.digikey.com/product-detail/en/panasonic-electronic-components/ERJ-3EKF1004V/P1.00MHCT-ND/198072)
R88 R89 R92 R93 | 1k | 1k |  |  | Digikey (https://www.digikey.com/product-detail/en/stackpole-electronics-inc/RNCP0603FTD1K00/RNCP0603FTD1K00CT-ND/2240445)
R7 | 200k | 200k |  |  | Digikey (https://www.digikey.com/product-detail/en/yageo/RC0603FR-07200KL/311-200KHRCT-ND/729991)
R35 R36 | 25m | 25m |  |  | Digikey (https://www.digikey.com/product-detail/en/panasonic-electronic-components/ERJ-6BWFR025V/P17580CT-ND/5648064)
R19 | 2k | 2k |  |  | Digikey (https://www.digikey.com/product-detail/en/yageo/RC0603FR-072KL/311-2.00KHRCT-ND/729956)
R58 R63 R68 | 45.2k | 45.3k |  |  | Digikey (https://www.digikey.com/product-detail/en/yageo/RC0603FR-0745K3L/311-45.3KHRCT-ND/730192)
R41 | 470 | 470 |  |  | Digikey (https://www.digikey.com/product-detail/en/rohm-semiconductor/ESR03EZPF4700/RHM470ADCT-ND/1983769)
R9 R14 R52 R53 | 510 | 510 |  |  | Digikey (https://www.digikey.com/product-detail/en/panasonic-electronic-components/ERJ-PA3F5100V/P510BYCT-ND/5036199)
R39 R40 R42 R60 R61 R82 | 80 | 80 |  |  | Digikey (https://www.digikey.com/product-detail/en/vishay-dale/CRCW060382R0FKEAHP/541-82.0SCT-ND/5326872)
 |  |  |  |  |  | 0 |  | 0.00
SW1 |  |  |  |  | Digikey (https://www.digikey.com/products/en?keywords=EG2201A)
 |  |  |  |  |  | 0 |  | 0.00
U12 |  |  | ABPMANN030PG2A3 |  | Digikey (https://www.digikey.com/products/en?keywords=ABPMANN030PG2A3)
U15 |  |  | BME280 |  | Digikey (https://www.digikey.com/product-detail/en/bosch-sensortec/BME280/828-1063-1-ND/6136314)
U16 |  |  | CCS811
U6 U8 |  |  | LDL1117S33R |  | Digikey (https://www.digikey.com/product-detail/en/stmicroelectronics/LDL1117S33R/497-17239-1-ND/7102079)
U5 |  |  | LDL1117S50R |  | Digikey (https://www.digikey.com/product-detail/en/stmicroelectronics/LDL1117S50R/497-17240-1-ND/7102080)
U14 |  |  | LIS331HH |  | Digikey (https://www.digikey.com/product-detail/en/stmicroelectronics/LIS331HH/497-10134-ND/2192659)
U13 |  |  | LSM9DS1 |  | Digikey (https://www.digikey.com/product-detail/en/stmicroelectronics/LSM9DS1TR/497-14946-1-ND/4988079)
U1 |  |  | LT6703-3 |  | Digikey (https://www.digikey.com/scripts/DkSearch/dksus.dll?Detail&itemSeq=261705920&uq=636626252162000973)
U7 U9 |  |  | LTC2992 |  | Digikey (https://www.digikey.com/product-detail/en/linear-technology-analog-devices/LTC2992IDE-PBF/LTC2992IDE-PBF-ND/7807747)
U2 |  |  | LTC3605 |  | Digikey (https://www.digikey.com/product-detail/en/linear-technology-analog-devices/LTC3605EUF-TRPBF/LTC3605EUF-TRPBFCT-ND/8024613)
U3 U4 U10 |  |  | LTC4358 |  | Digikey (https://www.digikey.com/product-detail/en/linear-technology-analog-devices/LTC4358IFE-PBF/LTC4358IFE-PBF-ND/1927805)
U18 |  |  | RFM69HCW |  | Digikey (https://www.digikey.com/scripts/DkSearch/dksus.dll?Detail&itemSeq=261706353&uq=636626258186448789)
U11 |  |  | Teensy3.6 |  | N/A
U17 |  |  | ublox_max-m8q |  | Digikey (https://www.digikey.com/product-detail/en/u-blox-america-inc/MAX-M8Q-0/672-1003-1-ND/6150666)
 |  |  |  |  |  | 0 |  | 0.00
ANTENNA |  |  |  |  | Digikey (https://www.digikey.com/product-detail/en/0600-00030/0600-00030-ND/1844858)
 |  |  |  |  |  | 0 |  | 0.00
 |  |  |  |  |  | Total Cost |  | 0.00

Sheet: Reference
RIT MSD P18104: Bad Habips - High Altitute Balloon Instrumentation Platform Main Board V2 BOM
Ref | Description | Manf Part Number | Manf | Footprint | Purchase Link | Quantity | Price | Sub Total
C1, C2, C4, C5, C6, C7, C10, C11, C26 | 10uF, 25V | GRM21BR61E106MA73L | Murata | 0805(2012 Metric) | Digikey (https://www.digikey.com/product-detail/en/murata-electronics-north-america/GRM21BR61E106MA73L/490-10748-1-ND/5251352) | 9 | 0.21000 | 1.89
C3, C8, C15, C25 | 1uF, 16V | CL21B105KOFNNNG | Samsung | 0805(2012 Metric) | Digikey (https://www.digikey.com/product-detail/en/samsung-electro-mechanics/CL21B105KOFNNNG/1276-6471-1-ND/5958099) | 4 | 0.10000 | 0.40
C9, C24, C33 | 1nF | C0805C102K5RACTU | Kemet | 0805(2012 Metric) | Digikey (https://www.digikey.com/product-detail/en/kemet/C0805C102K5RACTU/399-1147-1-ND/411422) | 3 | 0.10000 | 0.30
C12, C18, C20, C22, C23, C27, C28, C29 | 0.1uF, 16V | ECP-U1C104MA5 | Panasonic | 0805(2012 Metric) | Digikey (https://www.digikey.com/product-detail/en/panasonic-electronic-components/ECP-U1C104MA5/PCF1126CT-ND/285453) | 8 | 0.66000 | 5.28
C13 | 10pF, 50V | CC0805JRNPO9BN100 | Yageo | 0805(2012 Metric) | Digikey (https://www.digikey.com/product-detail/en/yageo/CC0805JRNPO9BN100/311-1099-1-ND/303009) | 1 | 0.10000 | 0.10
C14 | 47uF, 16V | EMK325BJ476MM-P | Taiyo Yuden | 1210 (3225 Metric) | Digikey (https://www.digikey.com/product-detail/en/taiyo-yuden/EMK325BJ476MM-P/587-5436-1-ND/7067112) | 1 | 0.71000 | 0.71
C16 | 1F, 5.5V | KR-5R5C105-R | Eaton | Through-Hole | Digikey (https://www.digikey.com/product-detail/en/eaton/KR-5R5C105-R/283-2810-ND/1556238) | 1 | 2.72000 | 2.72
C17, C32 | 10000pF, 16V | ECH-U1C103JX5 | Panasonic | 0805(2012 Metric) | Digikey (https://www.digikey.com/product-detail/en/panasonic-electronic-components/ECH-U1C103JX5/PCF1196CT-ND/353743) | 2 | 0.46000 | 0.92
C30, C31 | 22pF | C0805C220J5GACTU | Kemet | 0805(2012 Metric) | Digikey (https://www.digikey.com/product-detail/en/kemet/C0805C220J5GACTU/399-1113-1-ND/411388) | 2 | 0.10000 | 0.20
D1, D2, D6 | 18V, 1W Zener | SMAZ18-13-F | Diodes Inc | DO-214AC | Digikey (https://www.digikey.com/product-detail/en/diodes-incorporated/SMAZ18-13-F/SMAZ18-FDICT-ND/816042) | 3 | 0.50000 | 1.50
D3, D4, D11 | 40V, 5A Schottky | CDBA540-HF | Comchip | DO-214AC | Digikey (https://www.digikey.com/product-detail/en/comchip-technology/CDBA540-HF/641-1707-1-ND/5226090) | 3 | 0.49000 | 1.47
D5 | Green LED | VLMG21J2M1-GS08 | Vishay | 2-SMD, J-Lead | Digikey (https://www.digikey.com/product-detail/en/vishay-semiconductor-opto-division/VLMG21J2M1-GS08/VLMG21J2M1-GS08CT-ND/4895911) | 1 | 0.47000 | 0.47
D7, D9 | Green LED | APT2012LZGCK | Kingbright | 0805(2012 Metric) | Digikey (https://www.digikey.com/product-detail/en/kingbright/APT2012LZGCK/754-1939-1-ND/5177469) | 2 | 0.61000 | 1.22
D8, D10 | Blue LED | HSMR-C170 | Broadcom | 0805(2012 Metric) | Digikey (https://www.digikey.com/product-detail/en/broadcom-limited/HSMR-C170/516-1445-1-ND/637769) | 2 | 0.89000 | 1.78
D16, D31, D34 | Red LED | LTST-C171KRKT | Lite-On | 0805(2012 Metric) | Digikey (https://www.digikey.com/product-detail/en/lite-on-inc/LTST-C171KRKT/160-1427-1-ND/386800) | 3 | 0.31000 | 0.93
D19, D20, D21, D22, D23, D24, D25, D26, D27, D28, D29, D30 | TVS Diodes | MMQA5V6T1G | On Semi | SC-74 | Digikey (https://www.digikey.com/product-detail/en/on-semiconductor/MMQA5V6T1G/MMQA5V6T1GOSCT-ND/1139867) | 12 | 0.31800 | 3.82
J1, J2, J3, J6, J7, J11, J12, J16 | 4POS 3MM Micro-Fit 3.0 Horizontal | 0430450400 | Molex | Custom Through-Hole | Digikey (https://www.digikey.com/product-detail/en/molex-llc/0430450400/WM1814-ND/252527) | 8 | 1.35000 | 10.80
Mates for Above | 4POS 3MM Mating Micro-Fit 3.0 | 43025-0400 | Molex | In-Line | Digikey (https://www.digikey.com/product-detail/en/molex-llc/43025-0400/WM1784-ND/252497) | 8 | 0.40000 | 3.20
J4, J9 | 6POS 3MM Micro-Fit 3.0 Horizontal | 0430450600 | Molex | Custom Through-Hole | Digikey (https://www.digikey.com/product-detail/en/molex-llc/0430450600/WM1815-ND/252528) | 2 | 1.71000 | 3.42
Mates for Above | 6POS 3MM Mating Micro-Fit 3.0 | 43025-0600 | Molex | In-Line | Digikey (https://www.digikey.com/product-detail/en/molex-llc/43025-0600/WM1785-ND/252498) | 2 | 0.43000 | 0.86
J5 | 8POS 3MM Micro-Fit 3.0 Horizontal | 0430450800 | Molex | Custom Through-Hole | Digikey (https://www.digikey.com/product-detail/en/molex-llc/0430450800/WM1816-ND/252529) | 1 | 2.09000 | 2.09
Mates for Above | 8POS 3MM Mating Micro-Fit 3.0 | 43025-0800 | Molex | In-Line | Digikey (https://www.digikey.com/product-detail/en/molex-llc/43025-0800/WM1786-ND/252499) | 1 | 0.49000 | 0.49
J8, J10, J14, J15, J17 | 2POS Right Angle Vertical | 1586041-2 | TE Connect. | Custom Through-Hole | Digikey (https://www.digikey.com/product-detail/en/1586041-2/A30614-ND/701619) | 5 | 0.70000 | 3.50
Mates for Above | CONN RCPT HOUSING 2POS 4.2MM | 1586019-2 | TE Connect. | In-Line | Digikey (https://www.digikey.com/product-detail/en/te-connectivity-amp-connectors/1586019-2/A107333-ND/1131454) | 5 | 0.21000 | 1.05
J13 | 4POS JST-PH Vertical 2.54mm | 4330589508 | WGCD | 2.54MM Header | Amazon (https://smile.amazon.com/gp/product/B071XW2JND/ref=oh_aui_detailpage_o05_s00?ie=UTF8&psc=1) | 1 | 9.79000 | 9.79
J18 | 7POS JST-PH Vertical 2.54mm | 4330589508 | WGCD | 2.54MM Header
Mates for Above | Kit included mates and pins | 4330589508 | WGCD | In-Line
J21 | 2POS 3MM Micro-Fit 3.0 Horizontal | 0436500200 | Molex | Custom Through-Hole | Digikey (https://www.digikey.com/product-detail/en/molex-llc/0436500200/WM1860-ND/268989) | 1 | 0.91000 | 0.91
Mates for Above | 2POS 3MM Mating Micro-Fit 3.0 | 43645-0200 | Molex | In-Line | Digikey (https://www.digikey.com/product-detail/en/molex-llc/43645-0200/WM1845-ND/268974) | 1 | 0.31000 | 0.31
TE Pins | Mating Pins for TE Connector | 1586315-1 | TE Connect. | In-Line | Digikey (https://www.digikey.com/product-detail/en/te-connectivity-amp-connectors/1586315-1/A30642-ND/701647) | 50 | 0.04520 | 2.26
Molex Pins | Mating pins for Molex Connectors | 43030-0001 | Molex | In-Line | Digikey (https://www.digikey.com/product-detail/en/molex-llc/43030-0001/WM1837CT-ND/467810) | 100 | 0.08390 | 8.39
J19 | Headers - 1x2 | B01MQ48T2V | OCRTech | 2.54MM Header | Amazon (https://smile.amazon.com/OCR-Breakaway-Connector-Assortment-Arduino/dp/B01MQ48T2V) | 1 | 6.99000 | 6.99
 |  |  |  |  |  | 0 |  | 0.00
L1 | 6.8uH, 3.7A | NRS8040T6R8NJGJ | Taiyo Yuden | Nonstandard SMT | Digikey (https://www.digikey.com/product-detail/en/taiyo-yuden/NRS8040T6R8NJGJ/587-2979-1-ND/2666084) | 1 | 0.51000 | 0.51
 |  |  |  |  |  | 0 |  | 0.00
Q1 | N-CH, 30V, 20A | NTD20N03L27T4G | On Semi | DPAK | Digikey (https://www.digikey.com/product-detail/en/on-semiconductor/NTD20N03L27T4G/NTD20N03L27T4GOSCT-ND/921548) | 1 | 1.08000 | 1.08
Q2, Q4, Q17 | P-CH, 30V, 3.8A | DMP3099L-7 | Diodes Inc. | SOT-23-3 | Digikey (https://www.digikey.com/product-detail/en/diodes-incorporated/DMP3099L-7/DMP3099L-7DICT-ND/5218217) | 3 | 0.42 | 1.26
Q3, Q5, Q6, Q7, Q8, Q9, Q12, Q14, Q15, Q18 | N-CH, 30V, 500mA | NTR4003NT3G | ON Semi | SOT-23-3 | Digikey (https://www.digikey.com/product-detail/en/on-semiconductor/NTR4003NT3G/NTR4003NT3GOSCT-ND/1967271) | 10 | 0.29 | 2.92
 |  |  |  |  |  | 0 |  | 0.00
R1, R4, R6, R37, R38, R40, R41, R43, R44, R45, R46, R51, R52, R53, R61, R63, R64 | 10kΩ,, 0.4W | ESR10EZPJ103 | Rohm | 0805 (2012 Metric) | Digikey (https://www.digikey.com/product-detail/en/rohm-semiconductor/ESR10EZPJ103/RHM10KKCT-ND/1762952) | 17 | 0.09 | 1.48
R2 | 2Ω, 1%, 20W | PF1262-2RF1 | Riedon | TO126 | Digikey (https://www.digikey.com/scripts/DkSearch/dksus.dll?Detail&itemSeq=251921007&uq=636546449291790512) | 1 | 3.04000 | 3.04
R3, R35, R47, R48, R49, R59 | 10Ω, 5%, 2/5W | ESR10EZPJ100 | Rohm | 0805 (2012 Metric) | Digikey (https://www.digikey.com/product-detail/en/rohm-semiconductor/ESR10EZPJ100/RHM10KCT-ND/1762949) | 6 | 0.10 | 0.60
R5, R8, R9 | 10mΩ, 1%, 1W | WSLP0805R0100FEA18 | Vishay Dale | 0805 (2012 Metric) | Digikey (https://www.digikey.com/products/en/resistors/chip-resistor-surface-mount/52?k=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) | 3 | 1.08000 | 3.24
R7 | 100kΩ, 5%, 1/8W | RC0805JR-07100KL | Yageo | 0805 (2012 Metric) | Digikey (https://www.digikey.com/product-detail/en/yageo/RC0805JR-07100KL/311-100KARCT-ND/731186) | 1 | 0.10000 | 0.10
R10 | 40.2kΩ, 1%, 1/8W | RC0805FR-0740K2L | Yageo | 0805 (2012 Metric) | Digikey (https://www.digikey.com/product-detail/en/yageo/RC0805FR-0740K2L/311-40.2KCRCT-ND/730888) | 1 | 0.10000 | 0.10
R11 | 3.57kΩ, 1%, 1/8W | RC0805FR-073K57L | Yageo | 0805 (2012 Metric) | Digikey (https://www.digikey.com/product-detail/en/yageo/RC0805FR-073K57L/311-3.57KCRCT-ND/730772) | 1 | 0.10000 | 0.10
R12 | 10.5kΩ, 1%, 1/8W | RC0805FR-0710K5L | Yageo | 0805 (2012 Metric) | Digikey (https://www.digikey.com/product-detail/en/yageo/RC0805FR-0710K5L/311-10.5KCRCT-ND/730487) | 1 | 0.10000 | 0.10
R13 | 7.5kΩ, 1%, 1/8W | RC0805FR-077K5L | Yageo | 0805 (2012 Metric) | Digikey (https://www.digikey.com/product-detail/en/yageo/RC0805FR-077K5L/311-7.50KCRCT-ND/731063) | 1 | 0.10000 | 0.10
R14 | 11.8kΩ, 1%, 1/8W | RC0805FR-0711K8L | Yageo | 0805 (2012 Metric) | Digikey (https://www.digikey.com/product-detail/en/yageo/RC0805FR-0711K8L/311-11.8KCRCT-ND/730505) | 1 | 0.10000 | 0.10
R15 | 261kΩ, 1%, 1/8W | RC0805FR-07261KL | Yageo | 0805 (2012 Metric) | Digikey (https://www.digikey.com/product-detail/en/yageo/RC0805FR-07261KL/311-261KCRCT-ND/730723) | 1 | 0.10000 | 0.10
R16 | 35.7kΩ, 1%, 1/8W | RC0805FR-0735K7L | Yageo | 0805 (2012 Metric) | Digikey (https://www.digikey.com/product-detail/en/yageo/RC0805FR-0735K7L/311-35.7KCRCT-ND/730826) | 1 | 0.10000 | 0.10
R17 | 681kΩ, 1%, 1/8W | RC0805FR-07681KL | Yageo | 0805 (2012 Metric) | Digikey (https://www.digikey.com/product-detail/en/yageo/RC0805FR-07681KL/311-681KCRCT-ND/731051) | 1 | 0.10000 | 0.10
R18, R21, R24 | 102kΩ, 1%, 1/8W | RC0805FR-07102KL | Yageo | 0805 (2012 Metric) | Digikey (https://www.digikey.com/product-detail/en/yageo/RC0805FR-07102KL/311-102KCRCT-ND/730493) | 3 | 0.10000 | 0.30
R19 | 107kΩ, 1%, 1/8W | RC0805FR-07107KL | Yageo | 0805 (2012 Metric) | Digikey (https://www.digikey.com/product-detail/en/yageo/RC0805FR-07107KL/311-107KCRCT-ND/730497) | 1 | 0.10000 | 0.10
R20, R23 | 41.2kΩ, 1%, 1/8W | RC0805FR-0741K2L | Yageo | 0805 (2012 Metric) | Digikey (https://www.digikey.com/product-detail/en/yageo/RC0805FR-0741K2L/311-41.2KCRCT-ND/730892) | 2 | 0.10000 | 0.20
R22, R25, R29, R32 | 10.2kΩ, 1%, 1/8W | RC0805FR-0710K2L | Yageo | 0805 (2012 Metric) | Digikey (https://www.digikey.com/product-detail/en/yageo/RC0805FR-0710K2L/311-10.2KCRCT-ND/730485) | 4 | 0.10000 | 0.40
R26 | 75kΩ, 1%, 1/8W | RC0805FR-0775KL | Yageo | 0805 (2012 Metric) | Digikey (https://www.digikey.com/product-detail/en/yageo/RC0805FR-0775KL/311-75.0KCRCT-ND/731080) | 1 | 0.10000 | 0.10
R27 | 13.7kΩ, 1%, 1/8W | RC0805FR-0713K7L | Yageo | 0805 (2012 Metric) | Digikey (https://www.digikey.com/product-detail/en/yageo/RC0805FR-0713K7L/311-13.7KCRCT-ND/730535) | 1 | 0.10000 | 0.10
R28 | 18.7kΩ, 1%, 1/8W | RC0805FR-0718K7L | Yageo | 0805 (2012 Metric) | Digikey (https://www.digikey.com/product-detail/en/yageo/RC0805FR-0718K7L/311-18.7KCRCT-ND/730595) | 1 | 0.10000 | 0.10
R30, R33 | 43.2kΩ, 1%, 1/8W | RC0805FR-0743K2L | Yageo | 0805 (2012 Metric) | Digikey (https://www.digikey.com/product-detail/en/yageo/RC0805FR-0743K2L/311-43.2KCRCT-ND/730902) | 2 | 0.10000 | 0.20
R31, R34 | 15kΩ, 1%, 1/8W | RC0805FR-0715KL | Yageo | 0805 (2012 Metric) | Digikey (https://www.digikey.com/product-detail/en/yageo/RC0805FR-0715KL/311-15.0KCRCT-ND/730555) | 2 | 0.10000 | 0.20
R36, R54 | 1.2kΩ, 5%, 1/8W | RC0805FR-071K2L | Yageo | 0805 (2012 Metric) | Digikey (https://www.digikey.com/product-detail/en/yageo/RC0805FR-071K2L/311-1.20KCRCT-ND/730413) | 2 | 0.10000 | 0.20
R39, R55 | 100Ω, 5%, 1/8W | RC0805JR-07100RL | Yageo | 0805 (2012 Metric) | Digikey (https://www.digikey.com/product-detail/en/yageo/RC0805JR-07100RL/311-100ARCT-ND/731185) | 2 | 0.10000 | 0.20
R42, R57 | 150Ω, 5%, 1/8W | RC0805JR-07150RL | Yageo | 0805 (2012 Metric) | Digikey (https://www.digikey.com/product-detail/en/yageo/RC0805JR-07150RL/311-150ARCT-ND/731202) | 2 | 0.10000 | 0.20
R50 | 0, 1/8W | RC0805JR-070RL | Yageo | 0805 (2012 Metric) | Digikey (https://www.digikey.com/product-detail/en/yageo/RC0805JR-070RL/311-0.0ARCT-ND/731163) | 1 | 0.10000 | 0.10
R60 | 330Ω, 5%, 1/8W | RC0805JR-07330RL | Yageo | 0805 (2012 Metric) | Digikey (https://www.digikey.com/product-detail/en/yageo/RC0805JR-07330RL/311-330ARCT-ND/731258) | 1 | 0.10000 | 0.10
R62 | 910Ω, 5%, 1/8W | RC0805JR-07910RL | Yageo | 0805 (2012 Metric) | Digikey (https://www.digikey.com/product-detail/en/yageo/RC0805JR-07910RL/311-910ARCT-ND/731329) | 1 | 0.10000 | 0.10
 |  |  |  |  |  | 0 |  | 0.00
SW1, SW3 | TACTILE SPST-NO 0.05A 12V | PTS645SM43SMTR92 LFS | C & K | Nonstandard SMT | Digikey (https://www.digikey.com/product-detail/en/c-k/PTS645SM43SMTR92%20LFS/CKN9112CT-ND/1146934) | 2 | 0.16000 | 0.32
SW2, SW4 | SWITCH SLIDE DPDT 5A 120V | 500SDP1S1M2QEA | E-Switch | Throuh Hole | Digikey (https://www.digikey.com/scripts/DkSearch/dksus.dll?Detail&itemSeq=251921006&uq=636546479865490512) | 2 | 3.55000 | 7.10
 |  |  |  |  |  | 0 |  | 0.00
U1 | Dual Power Monitor | LTC2992IDE#PBF | Linear Tech | 16-DFN (4x3) | Digikey (https://www.digikey.com/product-detail/en/linear-technology-analog-devices/LTC2992IDE-PBF/LTC2992IDE-PBF-ND/7807747) | 1 | 9.64000 | 9.64
U2, U3 | Adjustable 1.5A LDO | AZ2117H-ADJTRG1 | Diodes Inc. | SOT-223 | Digikey (https://www.digikey.com/product-detail/en/AZ2117H-ADJTRG1/AZ2117H-ADJTRG1DICT-ND/7670077) | 2 | 0.40000 | 0.80
U4 | Switching Regulator | LT8609EMSE#PBF | Linear Tech | 10-TFSOP, 10-MSOP | Digikey (https://www.digikey.com/products/en?keywords=LT8609EMSE%23PBF) | 1 | 5.46 | 5.46
U5 | Teensy 3.6 | TEENSY36 | PJRC | DIP | PJRC (https://www.pjrc.com/store/teensy36.html) | 1 | 29.95000 | 29.95
U6 | IMU + Magnetometer | LSM9DS1TR | ST Micro | Nonstandard SMT | Digikey (https://www.digikey.com/product-detail/en/stmicroelectronics/LSM9DS1TR/497-14946-1-ND/4988079) | 1 | 6.33000 | 6.33
U7 | Temp/Pressure/Humidity Sensor | BME280 | Bosch | 8-LGA | Digikey (https://www.digikey.com/product-detail/en/bosch-sensortec/BME280/828-1063-1-ND/6136314) | 1 | 7.56 | 7.56
U8 | MCU 16BIT 256KB FRAM | MSP430FR5994IPNR | T.I. | 80LQFP | Digikey (https://www.digikey.com/product-detail/en/texas-instruments/MSP430FR5994IPNR/296-45561-1-ND/6826916) | 1 | 7.89000 | 7.89
U10, U11, U12 | TVS DIODE 2.5VWM 5VC | AOZ8318DI | A & O Semi | 10DFN | Digikey (https://www.digikey.com/product-detail/en/alpha-omega-semiconductor-inc/AOZ8318DI/785-1703-1-ND/5014273) | 3 | 0.91000 | 2.73
 |  |  |  |  |  | 0 |  | 0.00
Y1 | 32.7680kHZ Crystal | AB38T-32.768KHZ | Abracon | Through Hole | Digikey (https://www.digikey.com/product-detail/en/abracon-llc/AB38T-32.768KHZ/535-9034-ND/675229) | 1 | 0.17 | 0.17
Y2 | 24.000MHZ CMOS | ASEMB-24.000MHZ-LC-T | Abracon | 4-SMD | Digikey (https://www.digikey.com/product-detail/en/abracon-llc/ASEMB-24.000MHZ-LC-T/535-11748-1-ND/2809997) | 1 | 1.14000 | 1.14
 |  |  |  |  |  | 0 |  | 0.00
 |  |  |  |  |  | Total Cost |  | 174.48

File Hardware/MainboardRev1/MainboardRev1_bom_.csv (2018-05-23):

References | Value | Footprint | Quantity Per PCB | Datasheet
C4 C23 C32 C33 C34 C35 | .01uF | C_0603_HandSoldering | 6
C1 C5 C6 C14 C19 C24 C25 C26 C27 C28 C29 C30 C31 | 0.1uF | C_0603_HandSoldering | 13
C7 | 10pF | C_0603_HandSoldering | 1
C8 | 220pF | C_0603_HandSoldering | 1
C2 C3 C9 C10 C11 C12 C13 C15 C16 C17 C18 C20 C21 C22 | 47uF | C_1210_HandSoldering | 14
D5 | +3.3V_Zener | SOD-323_Diode | 1
D1 D2 | 5.6V | SOD-323_Diode | 2
D15 D17 | Blue | LED_0603_HandSoldering | 2
D3 | CMDSH2-3 | SOD-323_Diode | 1
D6 D7 D8 D9 D14 | Green | LED_0603_HandSoldering | 5
D10 D12 D13 D16 | Red | LED_0603_HandSoldering | 4
D4 D11 | SL42-E3/57T | DO-214AB_Zener | 2
J9 | 0733910320 [915MHz SMA] | CONN_RP-SMA_Right_Angle_0733910320 | 1
J1 | BACKUP_BATT: 1586038-2 | CONN_2POS_VERT_TE_CONN | 1
J14 | Buzzer | CONN_2POS_VERT_TE_CONN_LOCK_5-103669-1 | 1
J4 | EMATCH_1: 1586038-2 | CONN_2POS_VERT_TE_CONN | 1
J5 | EMATCH_2: 1586038-2 | CONN_2POS_VERT_TE_CONN | 1
J2 | MAIN_BATT: 1586038-2 | CONN_2POS_VERT_TE_CONN | 1
J3 | Servo_Control | Molex_Microfit3_Header_01x03_Straight | 1
J7 | Stratologger_DATA | 4-Pin_Molex_Vertical | 1
J6 | Stratologger_PWR: 1586038-2 | CONN_2POS_VERT_TE_CONN | 1
J15 | Strobe | CONN_2POS_VERT_TE_CONN_LOCK_5-103669-1 | 1
J10 | Switch_1 | CONN_2POS_VERT_TE_CONN_LOCK_5-103669-1 | 1
J12 | Switch_2 | CONN_2POS_VERT_TE_CONN_LOCK_5-103669-1 | 1
J11 | Switch_3 | CONN_2POS_VERT_TE_CONN_LOCK_5-103669-1 | 1
J13 | Switch_4 | CONN_2POS_VERT_TE_CONN_LOCK_5-103669-1 | 1
J8 | U.FL-R-SMT-1(10) | HRS_U.FL-R-SMT-1(10) | 1
L1 | RLF7030T-2R2M5R4 [2.2uH] | IND_RLF7030 | 1
Q5 Q6 Q7 Q9 Q11 Q12 Q13 Q14 Q16 Q19 Q20 Q23 Q24 Q25 Q27 Q30 Q31 | NTR4003 | SOT-23 | 17
Q21 Q22 | SIS612EDNT-T1-GE3 | PowerPAK_1212-8S | 2
Q1 Q2 Q3 Q4 Q8 Q10 Q15 Q17 Q18 Q26 Q28 Q29 | SSM3J328R | SOT-23 | 12
R80 | 0 | R_0603_HandSoldering | 1
R5 R24 R31 R72 R73 R74 R75 R76 R81 R83 | 10 | R_0603_HandSoldering | 10
R1 R2 R34 | 100k | R_0603_HandSoldering | 3
R4 R6 R8 R12 R13 R16 R18 R20 R21 R23 R44 R45 R46 R47 R50 R51 R54 R55 R65 R66 R67 R70 R71 R77 R79 R84 R85 R86 R87 R90 R91 R94 R95 R98 R99 | 10k | R_0603_HandSoldering | 35
R25 R28 | 10m | R_0805_HandSoldering | 2
R59 R64 R69 | 11.3k | R_0603_HandSoldering | 3
R27 R30 R33 R38 | 11.5k | R_0603_HandSoldering | 4
R17 | 118k | R_0603_HandSoldering | 1
R10 R11 R22 R48 R49 R78 R96 R97 | 12k | R_0603_HandSoldering | 8
R3 | 140k | R_0603_HandSoldering | 1
R43 R62 | 150 | R_0603_HandSoldering | 2
R15 | 16k | R_0603_HandSoldering | 1
R26 R29 R32 R37 R56 R57 | 1M | R_0603_HandSoldering | 6
R88 R89 R92 R93 | 1k | R_0603_HandSoldering | 4
R7 | 200k | R_0603_HandSoldering | 1
R35 R36 | 25m | R_0805_HandSoldering | 2
R19 | 2k | R_0603_HandSoldering | 1
R58 R63 R68 | 45.3k | R_0603_HandSoldering | 3
R41 | 470 | R_0603_HandSoldering | 1
R9 R14 R52 R53 | 510 | R_0603_HandSoldering | 4
R39 R40 R42 R60 R61 R82 | 80 | R_0603_HandSoldering | 6
SW1 | EG2201A [DPDT] | SW_DPDT_30V_200mA_EG2201A | 1
U12 | ABPMANN030PG2A3 | PRESSURE_TRANSDUCER_ABPMANN030PG2A3 | 1
U15 | BME280 | BME280 | 1
U16 | CCS811 | SON60P270X400X110-11N | 1
U6 U8 | LDL1117S33R | SOT-223_Tab_Pin_2 | 2 | http://www.st.com/st-web-ui/static/active/en/resource/technical/document/datasheet/CD00000544.pdf
U5 | LDL1117S50R | SOT-223_Tab_Pin_2 | 1 | http://www.st.com/st-web-ui/static/active/en/resource/technical/document/datasheet/CD00000544.pdf
U14 | LIS331HH | LGA16_3x3mm_0.5mm_pitch | 1
U13 | LSM9DS1 | PQFN24P43_350X300X102L35X23N | 1
U1 | LT6703-3 | SOT-23-5_HandSoldering | 1 | http://cds.linear.com/docs/en/datasheet/6106fb.pdf
U7 U9 | LTC2992 | DFN-16-1EP_3x4mm_Pitch0.45mm | 2
U2 | LTC3605 | QFN25_4x4mm_0.5mm_pitch | 1
U10 | LTC4358 | HTSSOP-16-1EP_4.4x5mm_Pitch0.65mm | 1
U3 U4 | LTC4358 | TSSOP-16-1EP_4.4x5mm_Pitch0.65mm | 2
U18 | RFM69HCW | RFM69HCW-XXXS2 | 1
U11 | Teensy3.6 | Teensy33_SidePinsAndVBatt | 1
U17 | ublox_max-m8q | MAX-M8 | 1

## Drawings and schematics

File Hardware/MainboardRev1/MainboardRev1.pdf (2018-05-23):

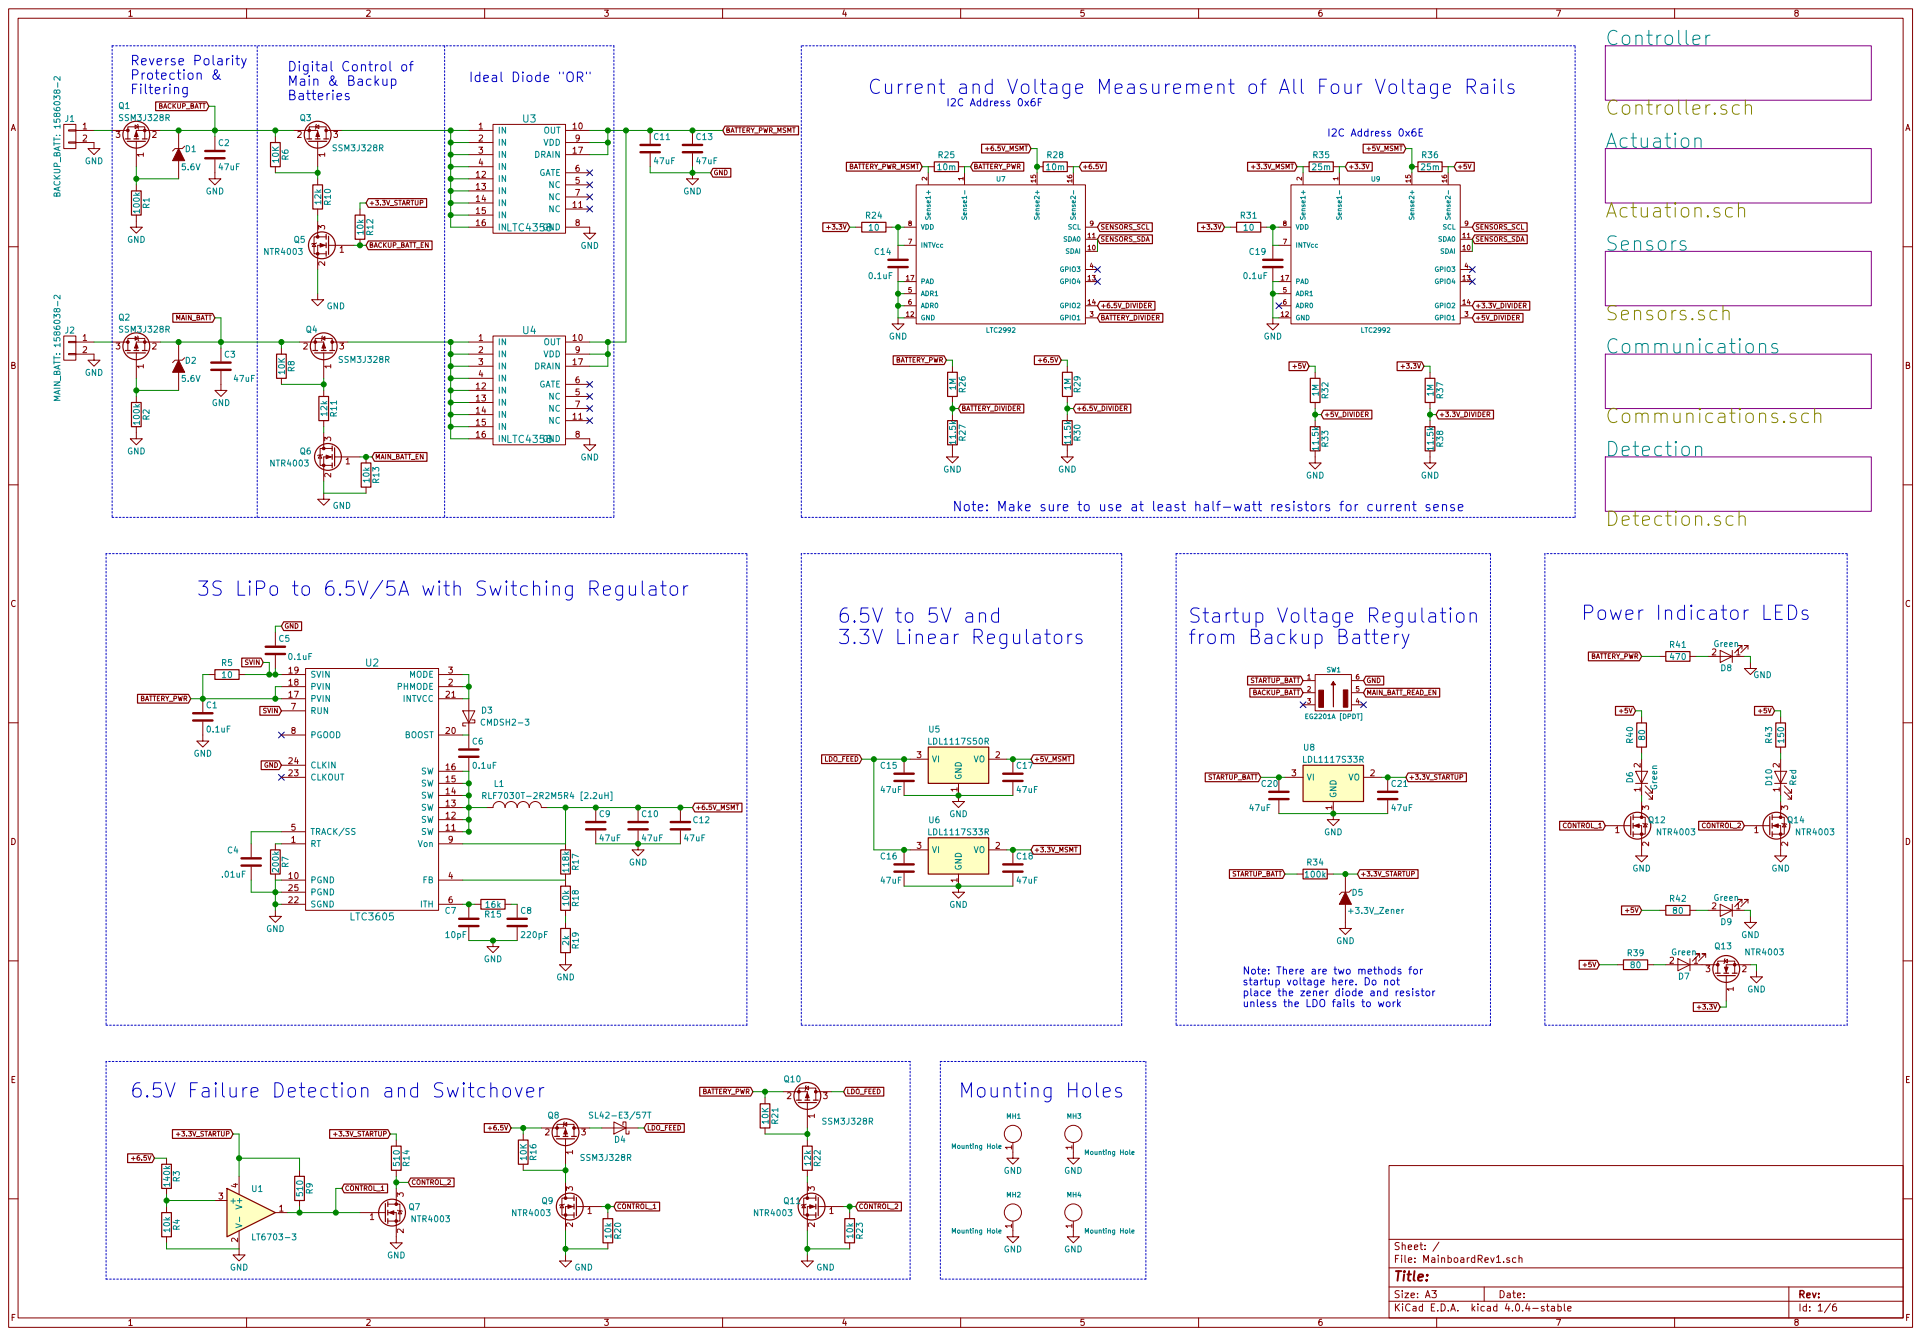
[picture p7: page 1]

Current and Voltage Measurement of All Four Voltage Rails
LTC2992 R25

Note: Make sure to use at least half-watt resistors for current sense GND

+3.3V_STARTUP Note: There are two methods for startup voltage here. Do not

place the zener diode and resistor
unless the LDO fails to work

LDO_FEED D4 SL42-E3/57T 6.5V Failure Detection and Switchover

1 MH1 Mounting Hole 1 MH3 Mounting Hole 1 MH2 Mounting Hole 1 MH4 Mounting Hole GND GND GND GND

Id: 1/6 Title: File: MainboardRev1.sch Sheet: /

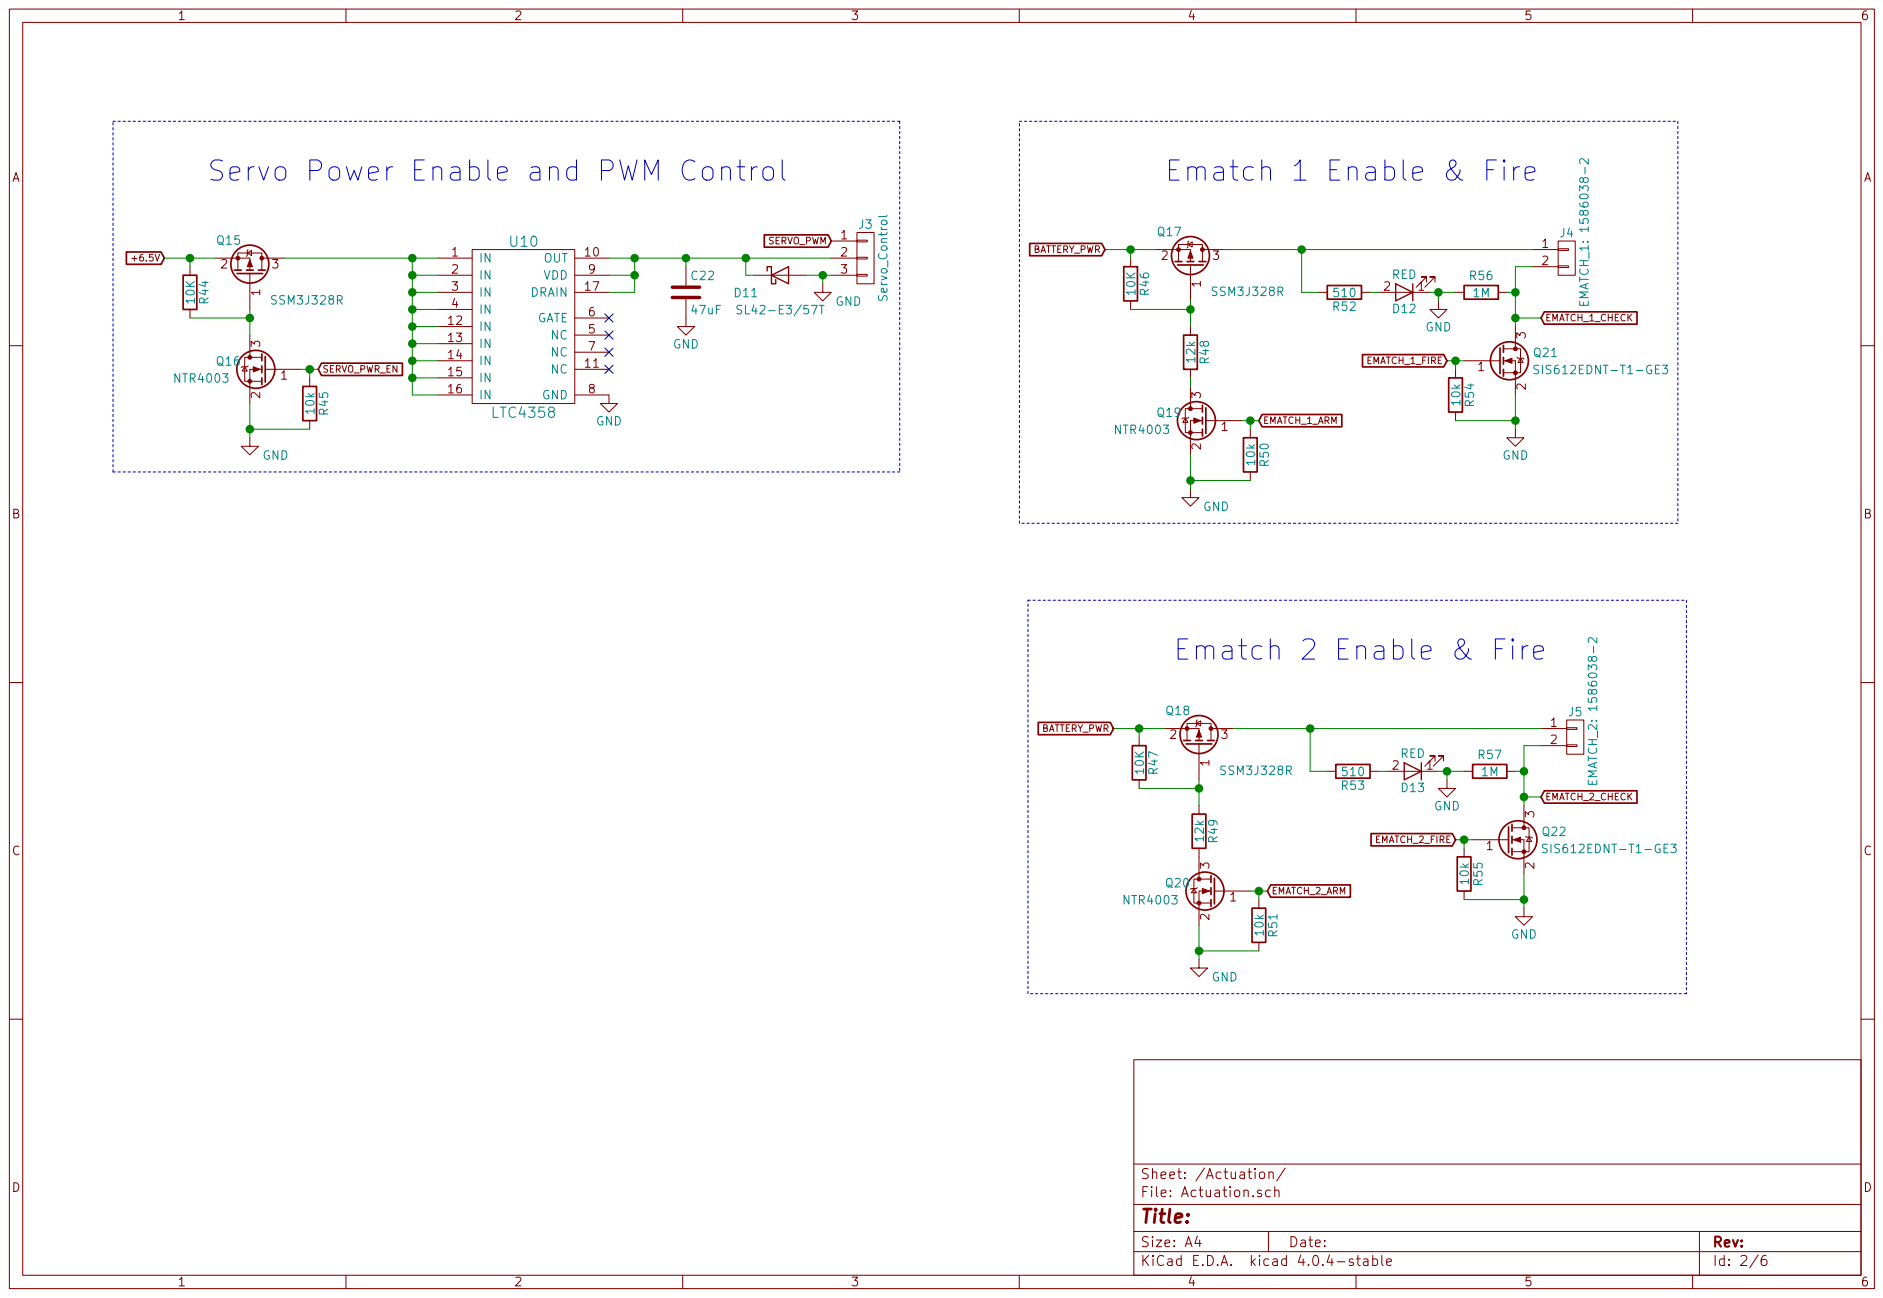
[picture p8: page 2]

Id: 2/6 Title: File: Actuation.sch Sheet: /Actuation/

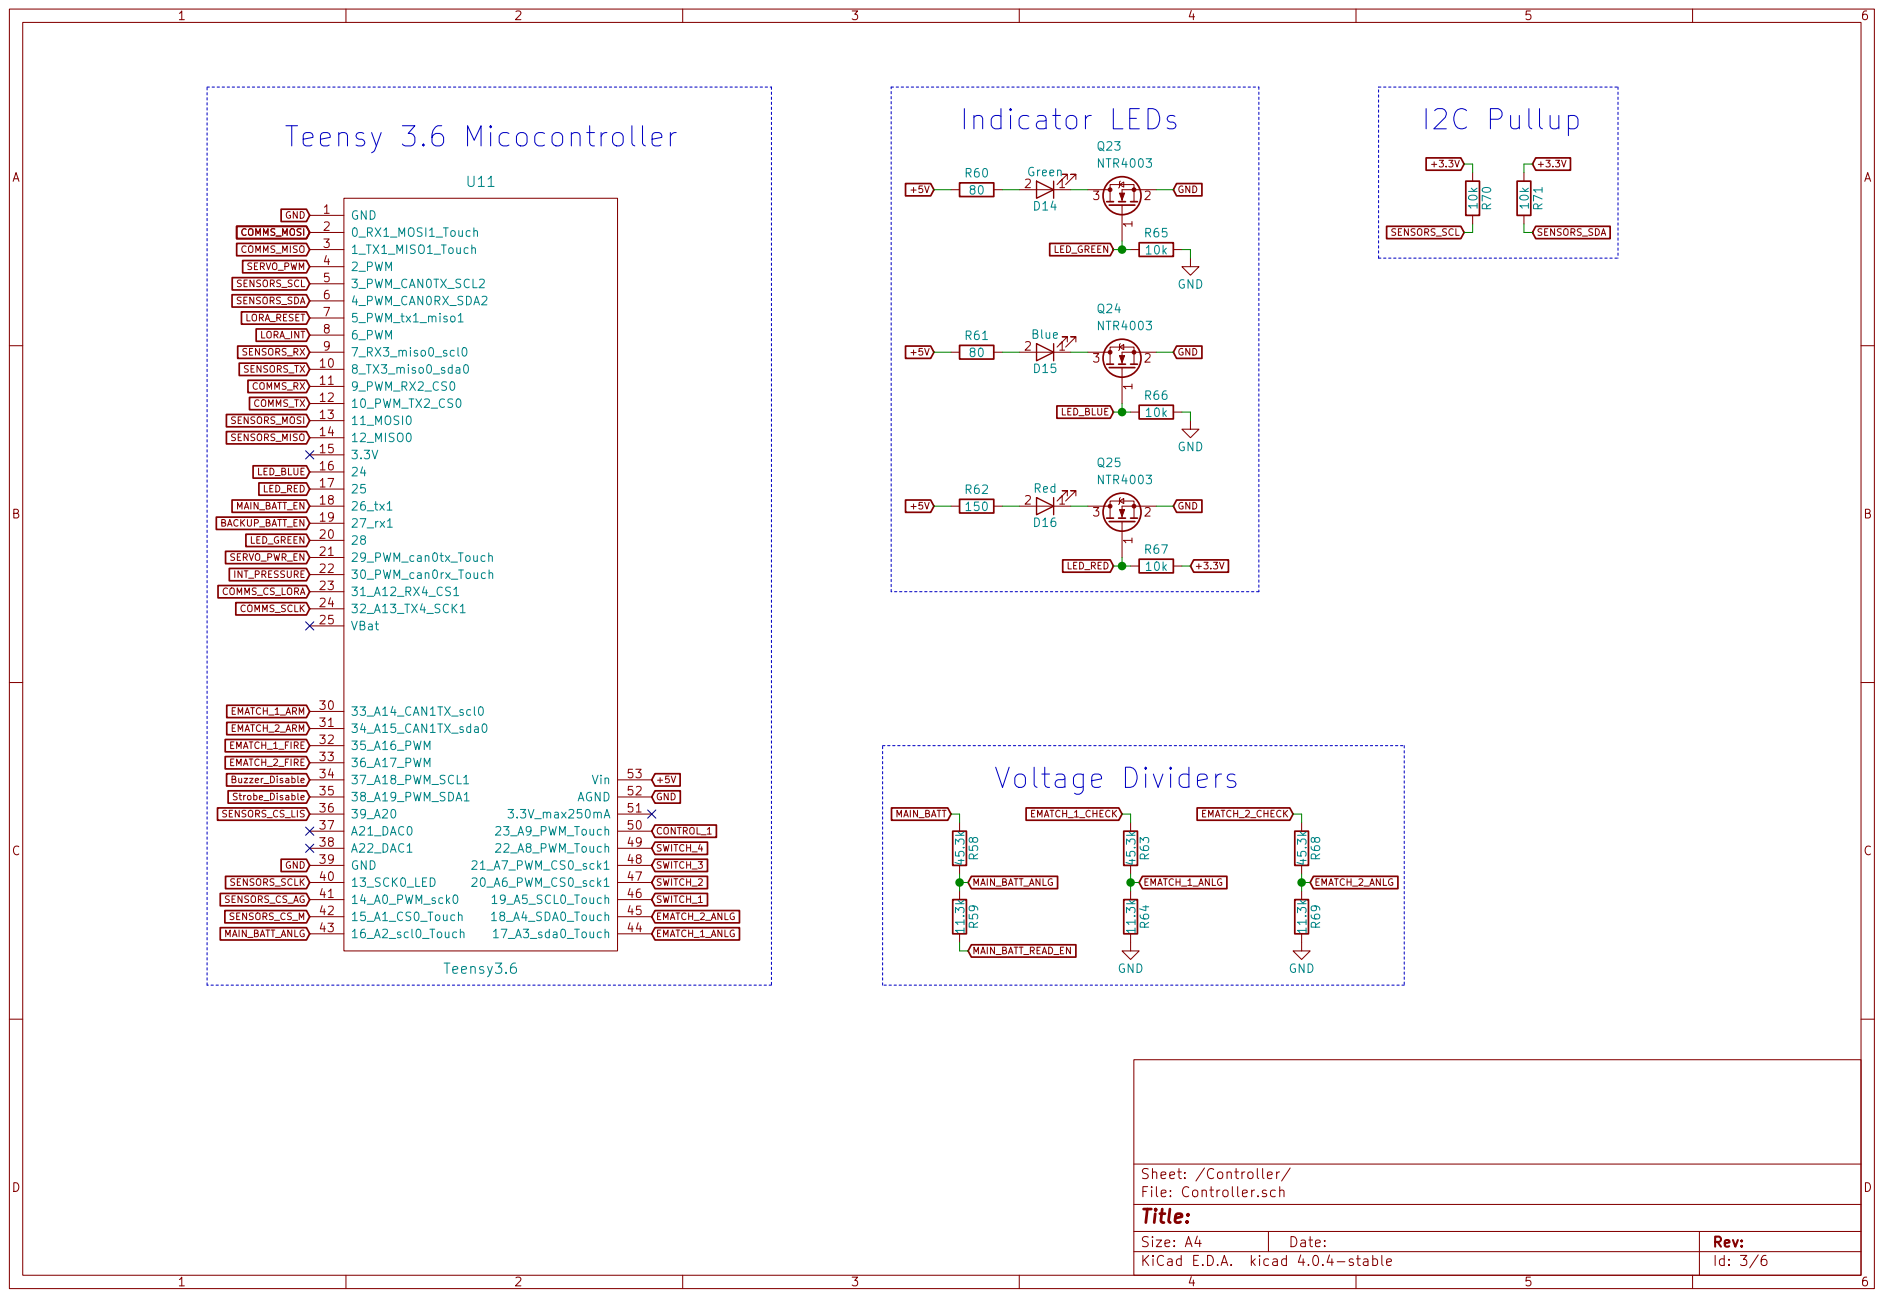
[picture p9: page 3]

Id: 3/6 Title: File: Controller.sch Sheet: /Controller/

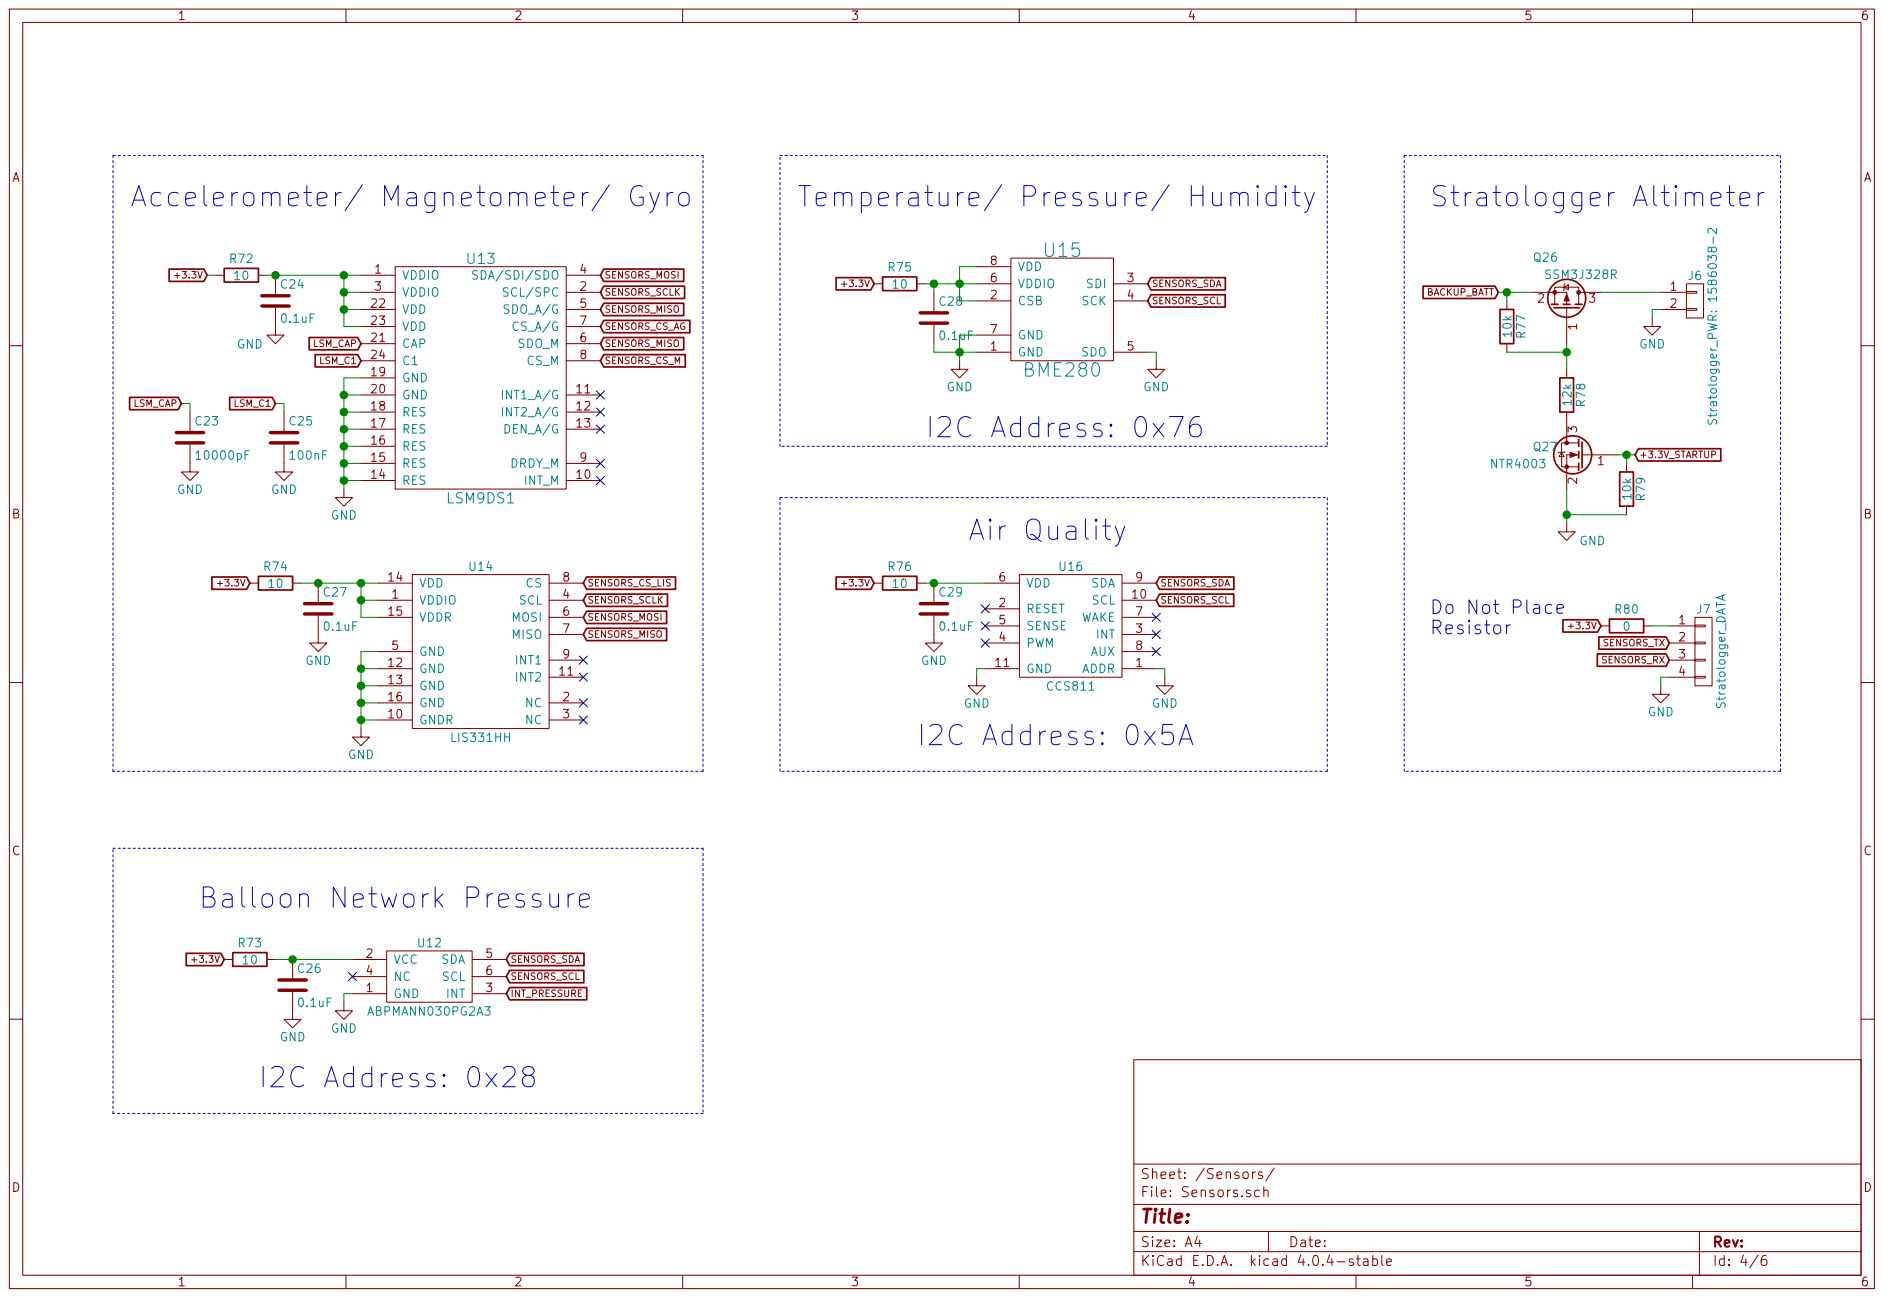
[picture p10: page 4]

Id: 4/6 Title: File: Sensors.sch Sheet: /Sensors/

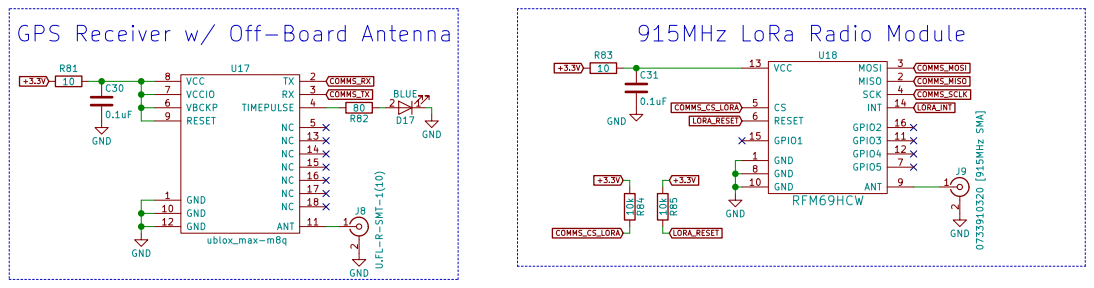
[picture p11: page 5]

Id: 5/6 Title: File: Communications.sch Sheet: /Communications/

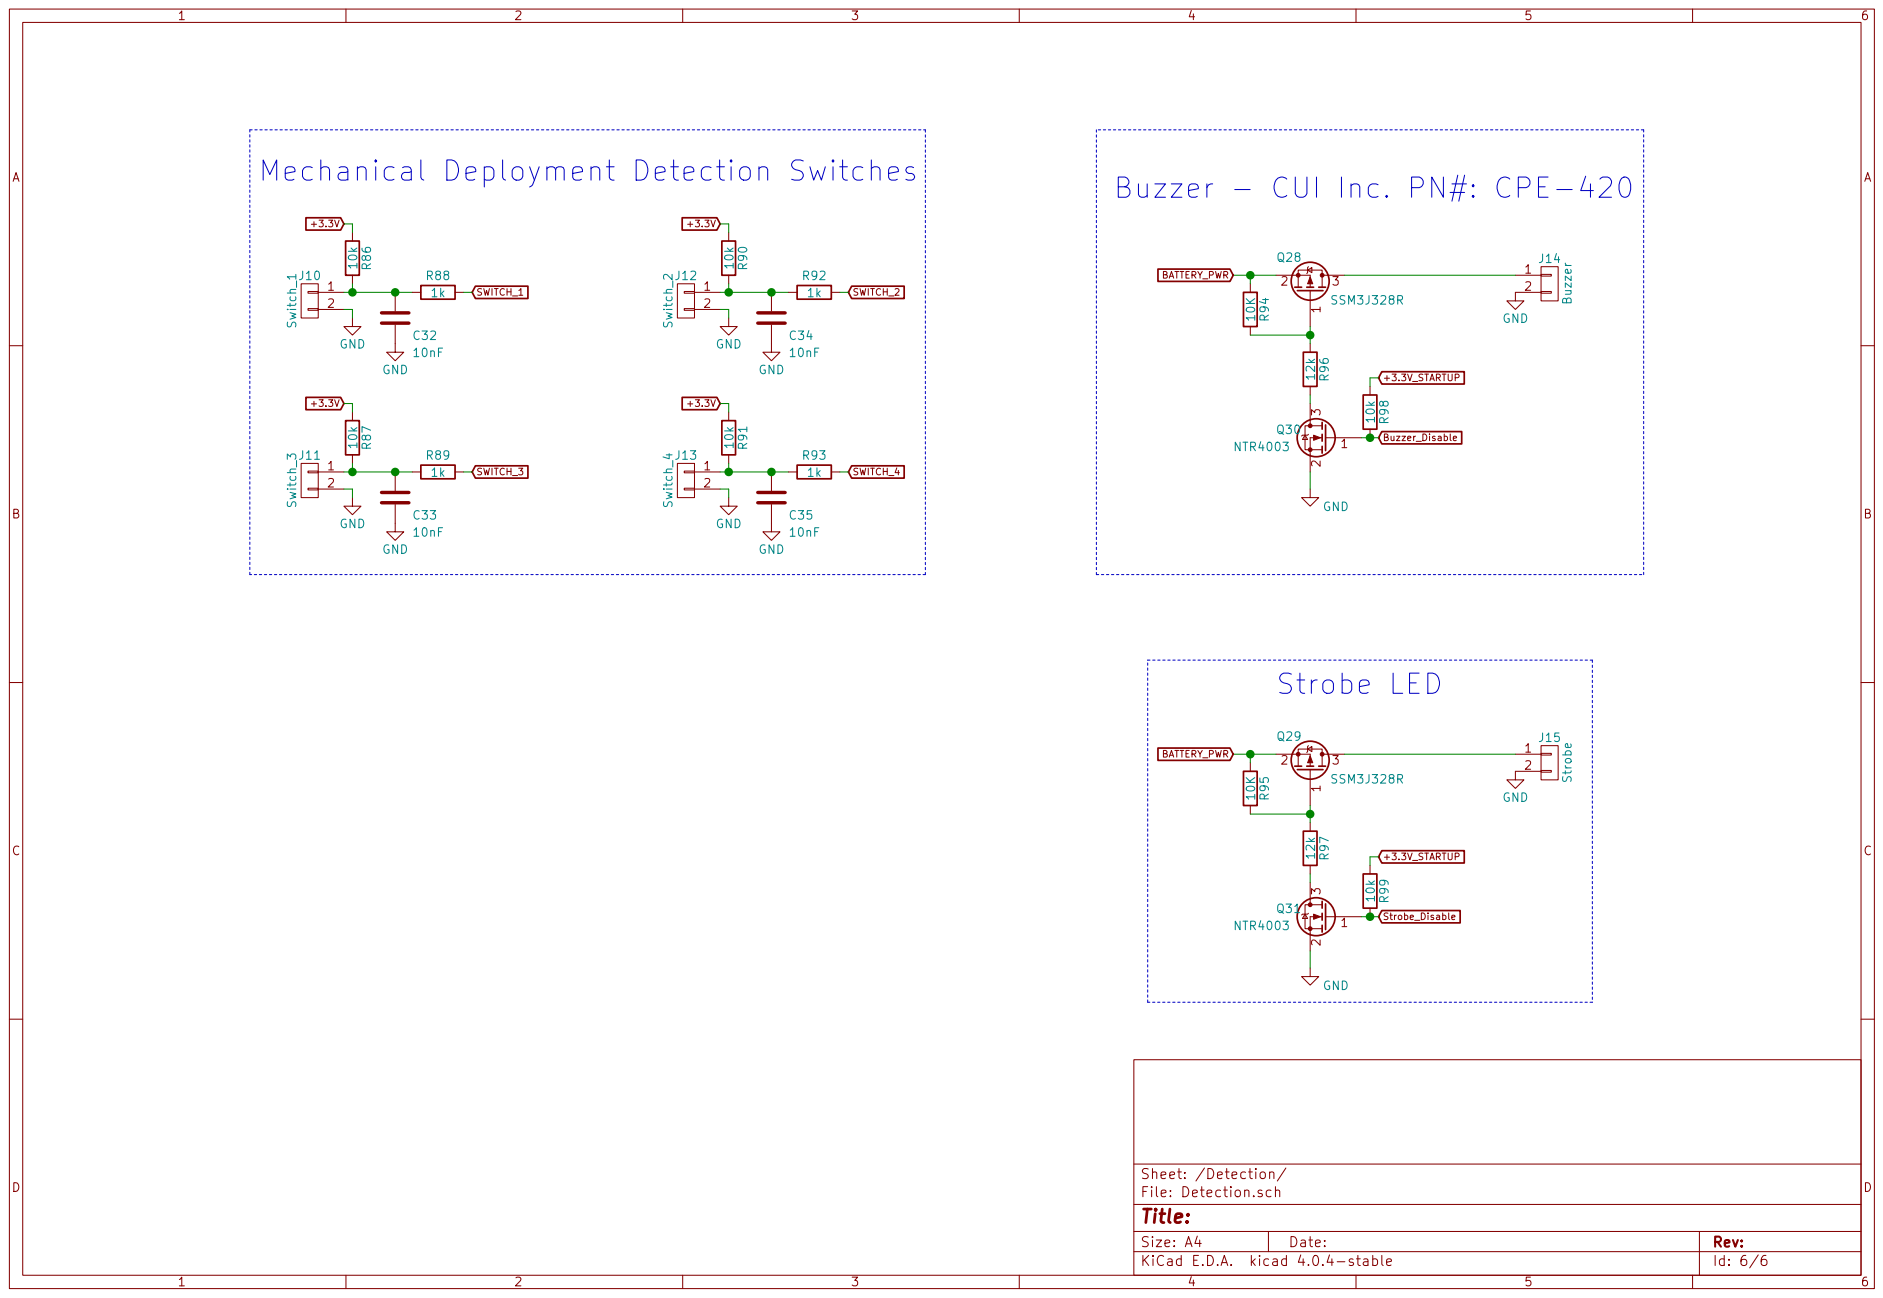
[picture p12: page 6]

+3.3V_STARTUP Buzzer - CUI Inc. PN#: CPE-420

Id: 6/6 Title: File: Detection.sch Sheet: /Detection/

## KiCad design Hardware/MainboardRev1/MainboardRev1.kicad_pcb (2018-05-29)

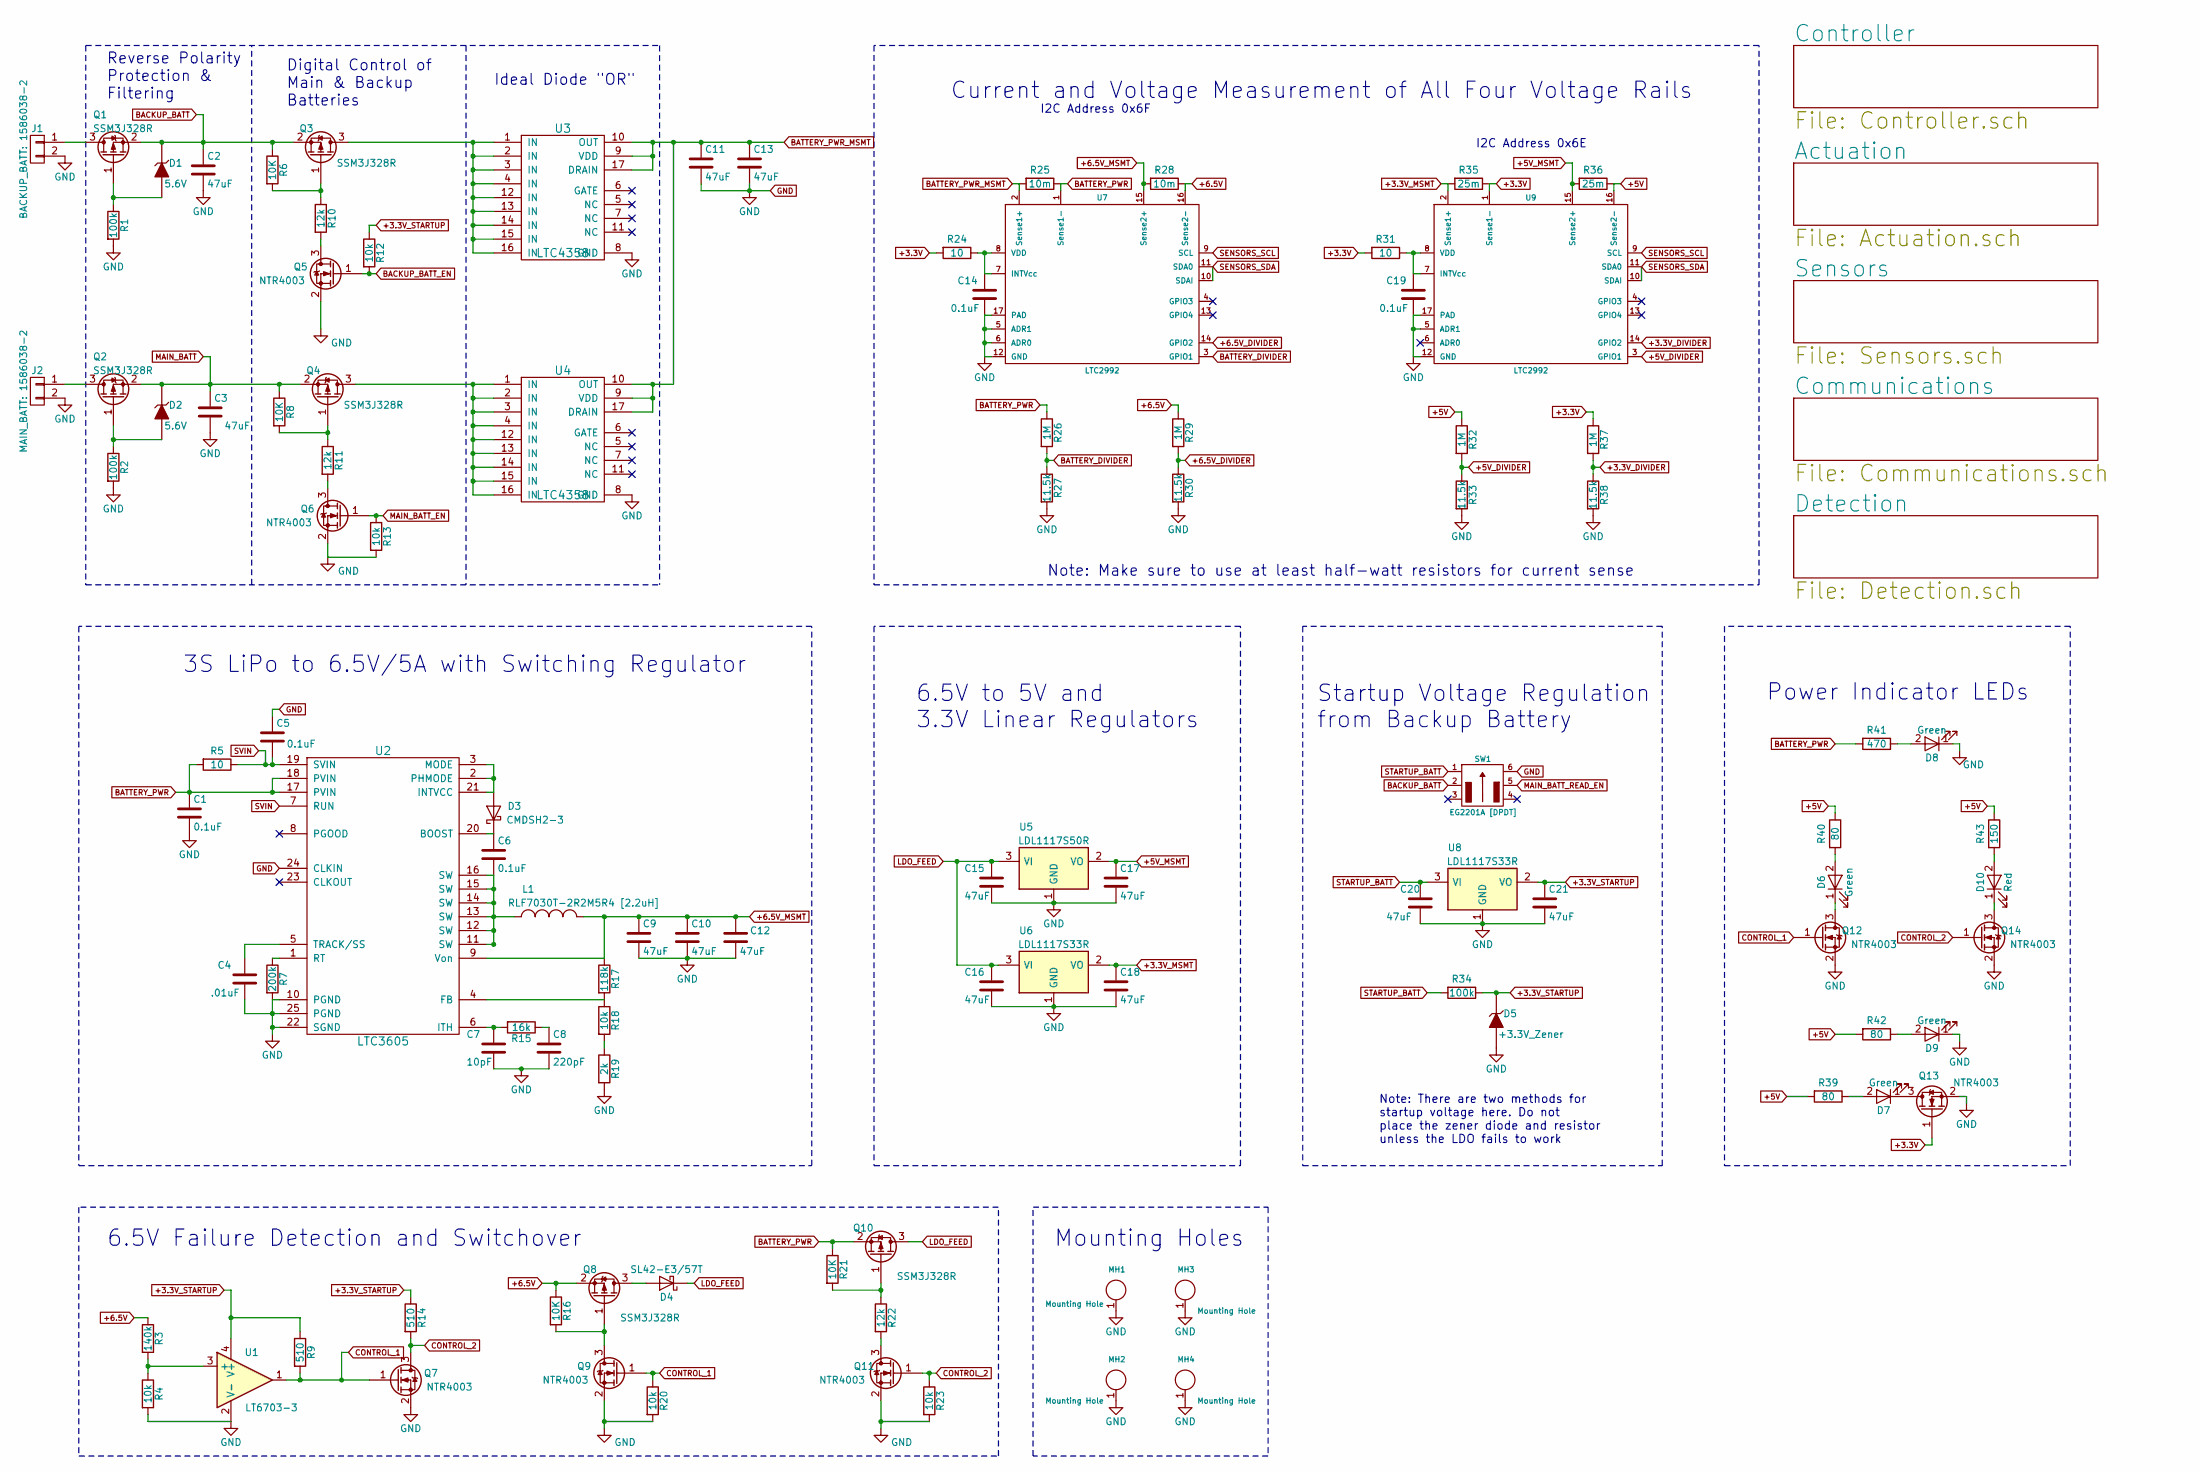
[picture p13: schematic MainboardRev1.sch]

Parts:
C1, C5, C6, C14, C19: 0.1uF; C_0603_HandSoldering
C2, C3, C9, C10, C11, C12, C13, C15, C16, C17, C18, C20, C21: 47uF; C_1210_HandSoldering
C4: .01uF; C_0603_HandSoldering
C7: 10pF; C_0603_HandSoldering
C8: 220pF; C_0603_HandSoldering
D1, D2: 5.6V; SOD-323_Diode
D3: CMDSH2-3; SOD-323_Diode
D4: SL42-E3/57T; DO-214AB_Zener
D5: +3.3V_Zener; SOD-323_Diode
D6, D7, D8, D9: Green; LED_0603_HandSoldering
D10: Red; LED_0603_HandSoldering
J1: BACKUP_BATT: 1586038-2; CONN_2POS_VERT_TE_CONN
J2: MAIN_BATT: 1586038-2; CONN_2POS_VERT_TE_CONN
L1: RLF7030T-2R2M5R4 [2.2uH]; IND_RLF7030
MH1, MH2, MH3, MH4: Mounting Hole; Mounting_Hole_3.50mm
Q1, Q2, Q3, Q4, Q8, Q10: SSM3J328R; SOT-23
Q5, Q6, Q7, Q9, Q11, Q12, Q13, Q14: NTR4003; SOT-23
R1, R2, R34: 100k; R_0603_HandSoldering
R3: 140k; R_0603_HandSoldering
R4, R12, R13, R18, R20, R23: 10k; R_0603_HandSoldering
R5, R24, R31: 10; R_0603_HandSoldering
R6, R8, R16, R21: 10K; R_0603_HandSoldering
R7: 200k; R_0603_HandSoldering
R9, R14: 510; R_0603_HandSoldering
R10, R11, R22: 12k; R_0603_HandSoldering
R15: 16k; R_0603_HandSoldering
R17: 118k; R_0603_HandSoldering
R19: 2k; R_0603_HandSoldering
R25, R28: 10m; R_0805_HandSoldering
R26, R29, R32, R37: 1M; R_0603_HandSoldering
R27, R30, R33, R38: 11.5k; R_0603_HandSoldering
R35, R36: 25m; R_0805_HandSoldering
R39, R40, R42: 80; R_0603_HandSoldering
R41: 470; R_0603_HandSoldering
R43: 150; R_0603_HandSoldering
SW1: EG2201A [DPDT]; SW_DPDT_30V_200mA_EG2201A
U1: LT6703-3; SOT-23-5_HandSoldering
U2: LTC3605; QFN25_4x4mm_0.5mm_pitch
U3, U4: LTC4358; TSSOP-16-1EP_4.4x5mm_Pitch0.65mm
U5: LDL1117S50R; SOT-223_Tab_Pin_2
U6, U8: LDL1117S33R; SOT-223_Tab_Pin_2
U7, U9: LTC2992; DFN-16-1EP_3x4mm_Pitch0.45mm

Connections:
+3.3V: Q13.1 (G), R24.2, R31.2, R35.1, R37.1, U9.1 (Sense1-); also elsewhere on the board
+3.3V_DIVIDER: R37.2, R38.1, U9.14 (GPIO2)
+3.3V_MSMT: C18.1, R35.2, U6.2 (VO), U9.2 (Sense1+)
+3.3V_STARTUP: C21.1, D5.1 (K), R9.1, R12.1, R14.1, R34.1, U1.4 (V+), U8.2 (VO); also elsewhere on the board
+5V: R32.1, R36.1, R39.2, R40.1, R42.2, R43.1, U9.16 (Sense2-); also elsewhere on the board
+5V_DIVIDER: R32.2, R33.1, U9.3 (GPIO1)
+5V_MSMT: C17.1, R36.2, U5.2 (VO), U9.15 (Sense2+)
+6.5V: Q8.2 (S), R3.1, R16.1, R28.1, R29.1, U7.16 (Sense2-); also elsewhere on the board
+6.5V_DIVIDER: R29.2, R30.1, U7.14 (GPIO2)
+6.5V_MSMT: C9.1, C10.1, C12.1, L1.2, R17.1, R28.2, U2.9 (Von), U7.15 (Sense2+)
BACKUP_BATT: C2.1, D1.1 (K), Q1.2 (S), Q3.2 (S), R6.1, SW1.2; also elsewhere on the board
BACKUP_BATT_EN: Q5.1 (G), R12.2; also elsewhere on the board
BATTERY_DIVIDER: R26.2, R27.1, U7.3 (GPIO1)
BATTERY_PWR: C1.1, Q10.2 (S), R5.2, R21.1, R25.1, R26.1, R41.2, U2.17 (PVIN), U2.18 (PVIN), U7.1 (Sense1-); also elsewhere on the board
BATTERY_PWR_MSMT: C11.1, C13.1, R25.2, U3.9 (VDD), U3.10 (OUT), U3.17 (DRAIN), U4.9 (VDD), U4.10 (OUT), U4.17 (DRAIN), U7.2 (Sense1+)
CONTROL_1: Q7.1 (G), Q9.1 (G), Q12.1 (G), R9.2, R20.1, U1.1; also elsewhere on the board
CONTROL_2: Q7.3 (D), Q11.1 (G), Q14.1 (G), R14.2, R23.1
GND: C1.2, C2.2, C3.2, C4.2, C5.1, C7.2, C8.2, C9.2, C10.2, C11.2, C12.2, C13.2, C14.2, C15.2, C16.2, C17.2, C18.2, C19.2, C20.2, C21.2, D5.2 (A), D8.1 (K), D9.1 (K), J1.2, J2.2, MH1.1, MH2.1, MH3.1, MH4.1, Q5.2 (S), Q6.2 (S), Q7.2 (S), Q9.2 (S), Q11.2 (S), Q12.2 (S), Q13.2 (S), Q14.2 (S), R1.2, R2.2, R4.2, R7.2, R13.2, R19.2, R20.2, R23.2, R27.2, R30.2, R33.2, R38.2, SW1.6, U1.2 (V-), U2.10 (PGND), U2.22 (SGND), U2.24 (CLKIN), U2.25 (PGND), U3.8 (GND), U4.8 (GND), U5.1 (GND), U6.1 (GND), U7.5 (ADR1), U7.6 (ADR0), U7.12 (GND), U7.17 (PAD), U8.1 (GND), U9.5 (ADR1), U9.12 (GND), U9.17 (PAD); also elsewhere on the board
LDO_FEED: C15.1, C16.1, D4.1 (K), Q10.3 (D), U5.3 (VI), U6.3 (VI)
MAIN_BATT: C3.1, D2.1 (K), Q2.2 (S), Q4.2 (S), R8.1; also elsewhere on the board
MAIN_BATT_EN: Q6.1 (G), R13.1; also elsewhere on the board
MAIN_BATT_READ_EN: SW1.5; also elsewhere on the board
unnamed: C4.1, U2.5 (TRACK/SS)
unnamed: C6.1, D3.1 (K), U2.20 (BOOST)
unnamed: C6.2, L1.1, U2.11 (SW), U2.12 (SW), U2.13 (SW), U2.14 (SW), U2.15 (SW), U2.16 (SW)
unnamed: C7.1, R15.2, U2.6 (ITH)
unnamed: C8.1, R15.1
unnamed: C14.1, R24.1, U7.7 (INTVcc), U7.8 (VDD)
unnamed: C19.1, R31.1, U9.7 (INTVcc), U9.8 (VDD)
unnamed: D1.2 (A), Q1.1 (G), R1.1
unnamed: D2.2 (A), Q2.1 (G), R2.1
unnamed 67: D3.2 (A), U2.2 (PHMODE), U2.3 (MODE), U2.21 (INTVCC); also elsewhere on the board
unnamed: D4.2 (A), Q8.3 (D)
unnamed: D6.1 (K), Q12.3 (D)
unnamed: D6.2 (A), R40.2
unnamed: D7.1 (K), Q13.3 (D)
unnamed: D7.2 (A), R39.1
unnamed: D8.2 (A), R41.1
unnamed: D9.2 (A), R42.1
unnamed: D10.1 (K), Q14.3 (D)
unnamed: D10.2 (A), R43.2
unnamed: J1.1, Q1.3 (D)
unnamed: J2.1, Q2.3 (D)
unnamed: Q3.1 (G), R6.2, R10.1
unnamed: Q3.3 (D), U3.1 (IN), U3.2 (IN), U3.3 (IN), U3.4 (IN), U3.12 (IN), U3.13 (IN), U3.14 (IN), U3.15 (IN), U3.16 (IN)
unnamed: Q4.1 (G), R8.2, R11.1
unnamed: Q4.3 (D), U4.1 (IN), U4.2 (IN), U4.3 (IN), U4.4 (IN), U4.12 (IN), U4.13 (IN), U4.14 (IN), U4.15 (IN), U4.16 (IN)
unnamed: Q5.3 (D), R10.2
unnamed: Q6.3 (D), R11.2
unnamed: Q8.1 (G), Q9.3 (D), R16.2
unnamed: Q10.1 (G), R21.2, R22.1
unnamed: Q11.3 (D), R22.2
unnamed: R3.2, R4.1, U1.3 (+)
unnamed: R7.1, U2.1 (RT)
unnamed: R17.2, R18.1, U2.4 (FB)
unnamed: R18.2, R19.1
SENSORS_SCL: U7.9 (SCL), U9.9 (SCL); also elsewhere on the board
SENSORS_SDA: U7.10 (SDAI), U7.11 (SDA0), U9.10 (SDAI), U9.11 (SDA0); also elsewhere on the board
STARTUP_BATT: C20.1, R34.2, SW1.1, U8.3 (VI)
SVIN: C5.2, R5.1, U2.7 (RUN), U2.19 (SVIN)

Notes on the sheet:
Reverse Polarity Protection & Filtering
Digital Control of Main & Backup Batteries
Ideal Diode "OR"
3S LiPo to 6.5V/5A with Switching Regulator
I2C Address 0x6F
I2C Address 0x6E
Current and Voltage Measurement of All Four Voltage Rails
Note: Make sure to use at least half-watt resistors for current sense
6.5V to 5V and 3.3V Linear Regulators
Note: There are two methods for startup voltage here. Do not place the zener diode and resistor unless the LDO fails to work
Startup Voltage Regulation from Backup Battery
Power Indicator LEDs
6.5V Failure Detection and Switchover
Mounting Holes

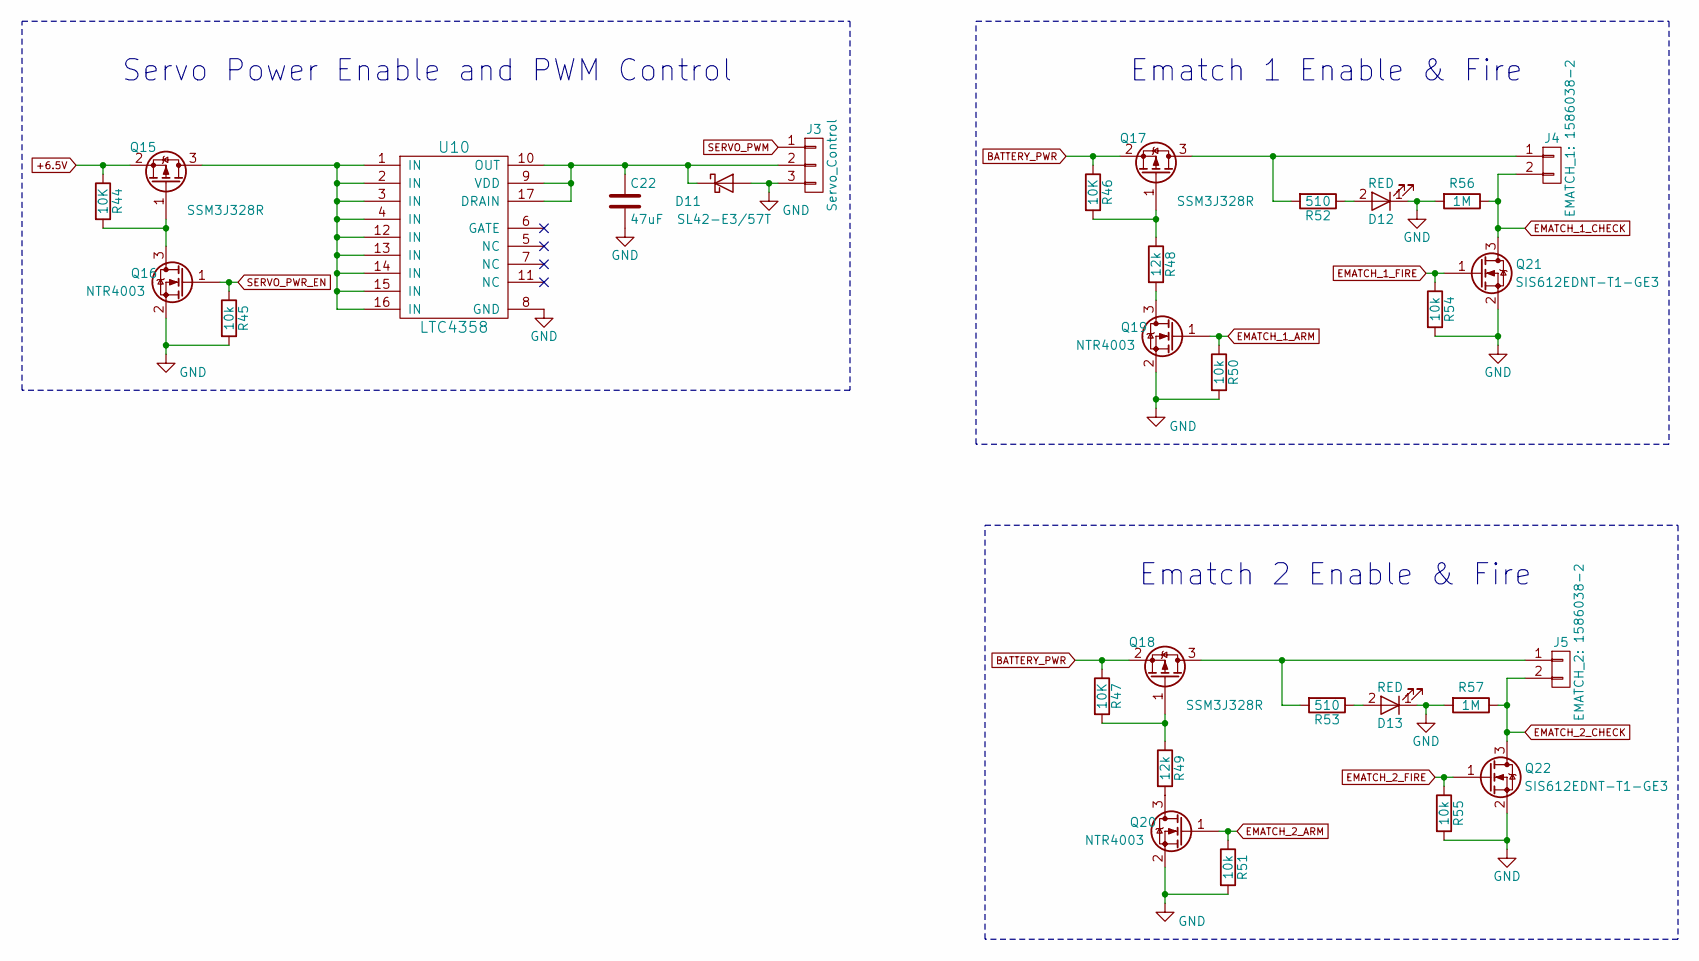
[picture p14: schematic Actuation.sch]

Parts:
C22: 47uF; C_1210_HandSoldering
D11: SL42-E3/57T; DO-214AB_Zener
D12, D13: RED; LED_0603_HandSoldering
J3: Servo_Control; Molex_Microfit3_Header_01x03_Straight
J4: EMATCH_1: 1586038-2; CONN_2POS_VERT_TE_CONN
J5: EMATCH_2: 1586038-2; CONN_2POS_VERT_TE_CONN
Q15, Q17, Q18: SSM3J328R; SOT-23
Q16, Q19, Q20: NTR4003; SOT-23
Q21, Q22: SIS612EDNT-T1-GE3; PowerPAK_1212-8S
R44, R46, R47: 10K; R_0603_HandSoldering
R45, R50, R51, R54, R55: 10k; R_0603_HandSoldering
R48, R49: 12k; R_0603_HandSoldering
R52, R53: 510; R_0603_HandSoldering
R56, R57: 1M; R_0603_HandSoldering
U10: LTC4358; HTSSOP-16-1EP_4.4x5mm_Pitch0.65mm

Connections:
+6.5V: Q15.2 (S), R44.1; also elsewhere on the board
BATTERY_PWR: Q17.2 (S), Q18.2 (S), R46.1, R47.1; also elsewhere on the board
EMATCH_1_ARM: Q19.1 (G), R50.1; also elsewhere on the board
EMATCH_1_CHECK: J4.2, Q21.3 (D), R56.1; also elsewhere on the board
EMATCH_1_FIRE: Q21.1 (G), R54.1; also elsewhere on the board
EMATCH_2_ARM: Q20.1 (G), R51.1; also elsewhere on the board
EMATCH_2_CHECK: J5.2, Q22.3 (D), R57.1; also elsewhere on the board
EMATCH_2_FIRE: Q22.1 (G), R55.1; also elsewhere on the board
GND: C22.2, D11.2 (A), D12.1 (K), D13.1 (K), J3.3, Q16.2 (S), Q19.2 (S), Q20.2 (S), Q21.2 (S), Q22.2 (S), R45.2, R50.2, R51.2, R54.2, R55.2, R56.2, R57.2, U10.8 (GND); also elsewhere on the board
unnamed: C22.1, D11.1 (K), J3.2, U10.9 (VDD), U10.10 (OUT), U10.17 (DRAIN)
unnamed: D12.2 (A), R52.1
unnamed: D13.2 (A), R53.1
unnamed: J4.1, Q17.3 (D), R52.2
unnamed: J5.1, Q18.3 (D), R53.2
unnamed: Q15.1 (G), Q16.3 (D), R44.2
unnamed: Q15.3 (D), U10.1 (IN), U10.2 (IN), U10.3 (IN), U10.4 (IN), U10.12 (IN), U10.13 (IN), U10.14 (IN), U10.15 (IN), U10.16 (IN)
unnamed: Q17.1 (G), R46.2, R48.1
unnamed: Q18.1 (G), R47.2, R49.1
unnamed: Q19.3 (D), R48.2
unnamed: Q20.3 (D), R49.2
SERVO_PWM: J3.1; also elsewhere on the board
SERVO_PWR_EN: Q16.1 (G), R45.1; also elsewhere on the board

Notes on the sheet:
Servo Power Enable and PWM Control
Ematch 1 Enable & Fire
Ematch 2 Enable & Fire

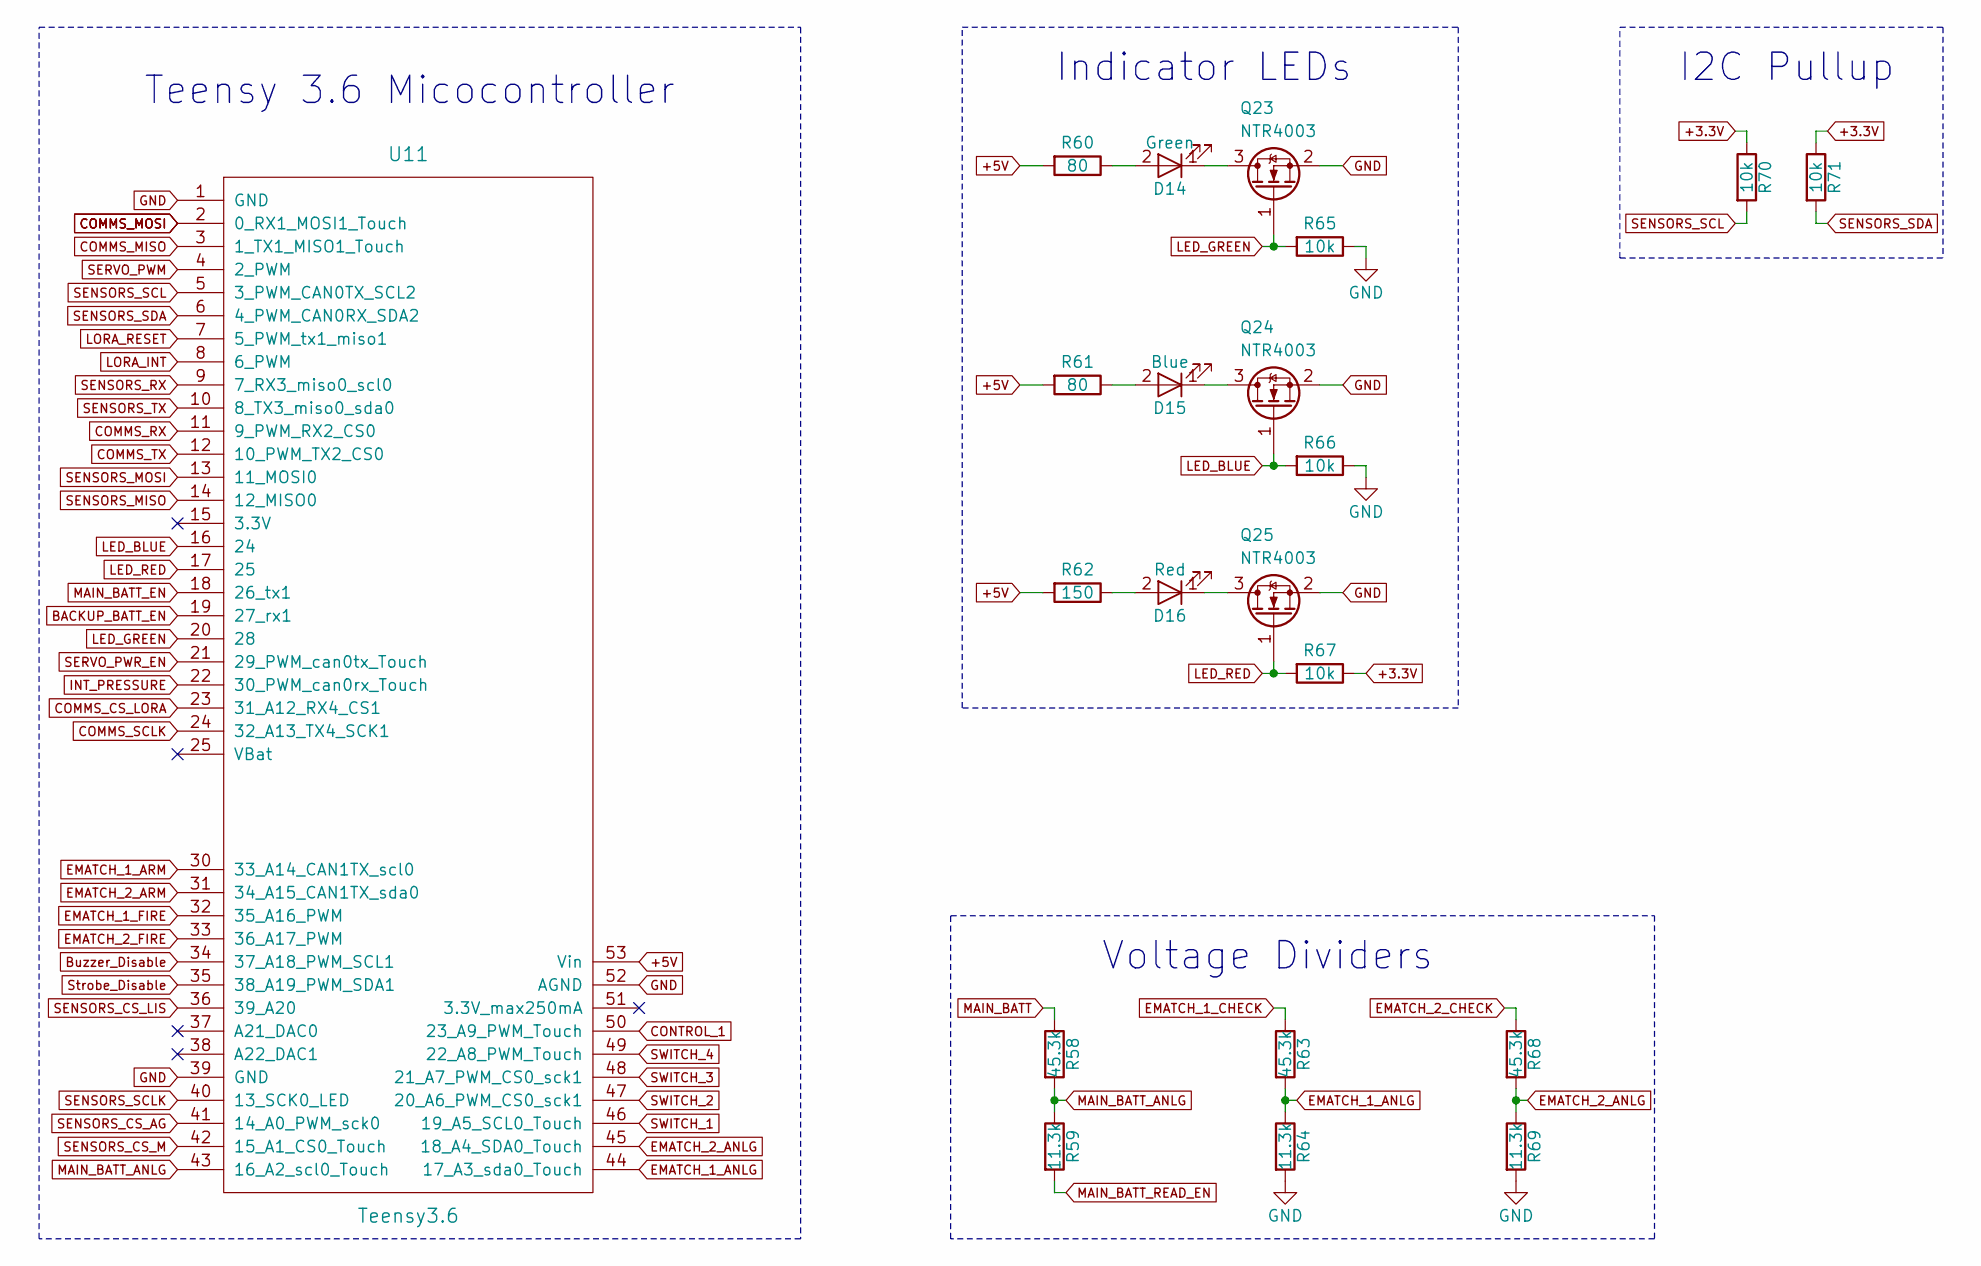
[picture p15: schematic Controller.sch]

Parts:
D14: Green; LED_0603_HandSoldering
D15: Blue; LED_0603_HandSoldering
D16: Red; LED_0603_HandSoldering
Q23, Q24, Q25: NTR4003; SOT-23
R58, R63, R68: 45.3k; R_0603_HandSoldering
R59, R64, R69: 11.3k; R_0603_HandSoldering
R60, R61: 80; R_0603_HandSoldering
R62: 150; R_0603_HandSoldering
R65, R66, R67, R70, R71: 10k; R_0603_HandSoldering
U11: Teensy3.6; Teensy33_SidePinsAndVBatt

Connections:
+3.3V: R67.1, R70.1, R71.1; also elsewhere on the board
+5V: R60.2, R61.2, R62.2, U11.53 (Vin); also elsewhere on the board
BACKUP_BATT_EN: U11.19 (27_rx1); also elsewhere on the board
Buzzer_Disable: U11.34 (37_A18_PWM_SCL1); also elsewhere on the board
COMMS_CS_LORA: U11.23 (31_A12_RX4_CS1); also elsewhere on the board
COMMS_MISO: U11.3 (1_TX1_MISO1_Touch); also elsewhere on the board
COMMS_MOSI: U11.2 (0_RX1_MOSI1_Touch); also elsewhere on the board
COMMS_RX: U11.11 (9_PWM_RX2_CS0); also elsewhere on the board
COMMS_SCLK: U11.24 (32_A13_TX4_SCK1); also elsewhere on the board
COMMS_TX: U11.12 (10_PWM_TX2_CS0); also elsewhere on the board
CONTROL_1: U11.50 (23_A9_PWM_Touch); also elsewhere on the board
EMATCH_1_ANLG: R63.2, R64.1, U11.44 (17_A3_sda0_Touch)
EMATCH_1_ARM: U11.30 (33_A14_CAN1TX_scl0); also elsewhere on the board
EMATCH_1_CHECK: R63.1; also elsewhere on the board
EMATCH_1_FIRE: U11.32 (35_A16_PWM); also elsewhere on the board
EMATCH_2_ANLG: R68.2, R69.1, U11.45 (18_A4_SDA0_Touch)
EMATCH_2_ARM: U11.31 (34_A15_CAN1TX_sda0); also elsewhere on the board
EMATCH_2_CHECK: R68.1; also elsewhere on the board
EMATCH_2_FIRE: U11.33 (36_A17_PWM); also elsewhere on the board
GND: Q23.2 (S), Q24.2 (S), Q25.2 (S), R64.2, R65.1, R66.1, R69.2, U11.1 (GND), U11.39 (GND), U11.52 (AGND); also elsewhere on the board
INT_PRESSURE: U11.22 (30_PWM_can0rx_Touch); also elsewhere on the board
LED_BLUE: Q24.1 (G), R66.2, U11.16 (24)
LED_GREEN: Q23.1 (G), R65.2, U11.20 (28)
LED_RED: Q25.1 (G), R67.2, U11.17 (25)
LORA_INT: U11.8 (6_PWM); also elsewhere on the board
LORA_RESET: U11.7 (5_PWM_tx1_miso1); also elsewhere on the board
MAIN_BATT: R58.1; also elsewhere on the board
MAIN_BATT_ANLG: R58.2, R59.1, U11.43 (16_A2_scl0_Touch)
MAIN_BATT_EN: U11.18 (26_tx1); also elsewhere on the board
MAIN_BATT_READ_EN: R59.2; also elsewhere on the board
unnamed: D14.1 (K), Q23.3 (D)
unnamed: D14.2 (A), R60.1
unnamed: D15.1 (K), Q24.3 (D)
unnamed: D15.2 (A), R61.1
unnamed: D16.1 (K), Q25.3 (D)
unnamed: D16.2 (A), R62.1
SENSORS_CS_AG: U11.41 (14_A0_PWM_sck0); also elsewhere on the board
SENSORS_CS_LIS: U11.36 (39_A20); also elsewhere on the board
SENSORS_CS_M: U11.42 (15_A1_CS0_Touch); also elsewhere on the board
SENSORS_MISO: U11.14 (12_MISO0); also elsewhere on the board
SENSORS_MOSI: U11.13 (11_MOSI0); also elsewhere on the board
SENSORS_RX: U11.9 (7_RX3_miso0_scl0); also elsewhere on the board
SENSORS_SCL: R70.2, U11.5 (3_PWM_CAN0TX_SCL2); also elsewhere on the board
SENSORS_SCLK: U11.40 (13_SCK0_LED); also elsewhere on the board
SENSORS_SDA: R71.2, U11.6 (4_PWM_CAN0RX_SDA2); also elsewhere on the board
SENSORS_TX: U11.10 (8_TX3_miso0_sda0); also elsewhere on the board
SERVO_PWM: U11.4 (2_PWM); also elsewhere on the board
SERVO_PWR_EN: U11.21 (29_PWM_can0tx_Touch); also elsewhere on the board
SWITCH_1: U11.46 (19_A5_SCL0_Touch); also elsewhere on the board
SWITCH_2: U11.47 (20_A6_PWM_CS0_sck1); also elsewhere on the board
SWITCH_3: U11.48 (21_A7_PWM_CS0_sck1); also elsewhere on the board
SWITCH_4: U11.49 (22_A8_PWM_Touch); also elsewhere on the board
Strobe_Disable: U11.35 (38_A19_PWM_SDA1); also elsewhere on the board

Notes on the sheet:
Teensy 3.6 Micocontroller
Indicator LEDs
I2C Pullup
Voltage Dividers

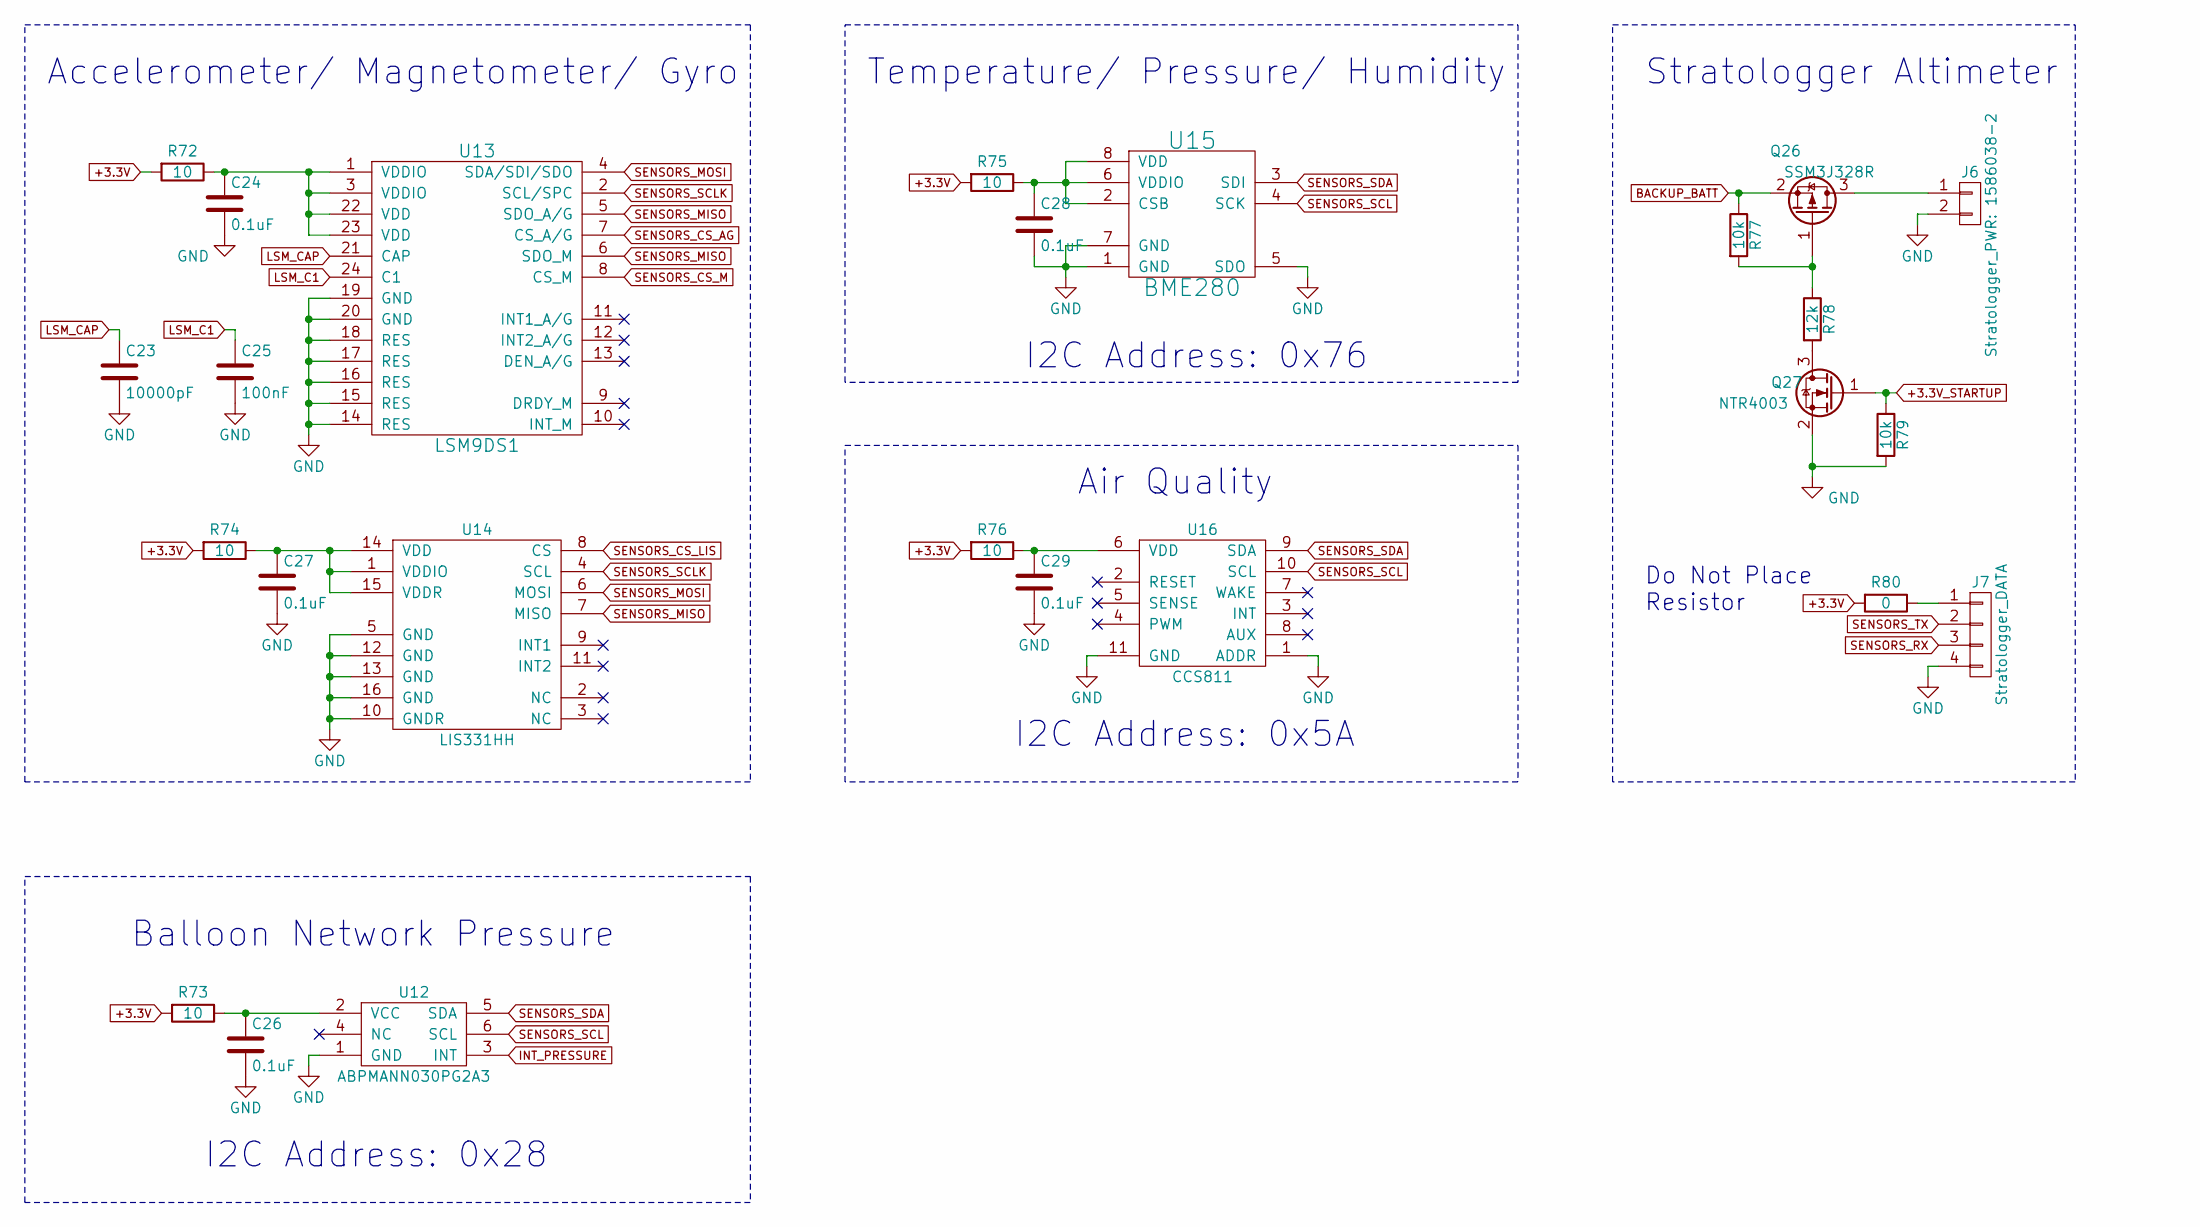
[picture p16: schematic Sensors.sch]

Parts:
C23: 10000pF; C_0603_HandSoldering
C24, C26, C27, C28, C29: 0.1uF; C_0603_HandSoldering
C25: 100nF; C_0603_HandSoldering
J6: Stratologger_PWR: 1586038-2; CONN_2POS_VERT_TE_CONN_LOCK_5-103669-1
J7: Stratologger_DATA; 4-Pin_Molex_Vertical
Q26: SSM3J328R; SOT-23
Q27: NTR4003; SOT-23
R72, R73, R74, R75, R76: 10; R_0603_HandSoldering
R77, R79: 10k; R_0603_HandSoldering
R78: 12k; R_0603_HandSoldering
R80: 0; R_0603_HandSoldering
U12: ABPMANN030PG2A3; PRESSURE_TRANSDUCER_ABPMANN030PG2A3
U13: LSM9DS1; PQFN24P43_350X300X102L35X23N
U14: LIS331HH; LGA16_3x3mm_0.5mm_pitch
U15: BME280
U16: CCS811; SON60P270X400X110-11N

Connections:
+3.3V: R72.2, R73.2, R74.2, R75.2, R76.2, R80.2; also elsewhere on the board
+3.3V_STARTUP: Q27.1 (G), R79.1; also elsewhere on the board
BACKUP_BATT: Q26.2 (S), R77.1; also elsewhere on the board
GND: C23.2, C24.2, C25.2, C26.2, C27.2, C28.2, C29.2, J6.2, J7.4, Q27.2 (S), R79.2, U12.1 (GND), U13.14 (RES), U13.15 (RES), U13.16 (RES), U13.17 (RES), U13.18 (RES), U13.19 (GND), U13.20 (GND), U14.5 (GND), U14.10 (GNDR), U14.12 (GND), U14.13 (GND), U14.16 (GND), U15.1 (GND), U15.5 (SDO), U15.7 (GND), U16.1 (ADDR), U16.11 (GND); also elsewhere on the board
INT_PRESSURE: U12.3 (INT); also elsewhere on the board
LSM_C1: C25.1, U13.24 (C1)
LSM_CAP: C23.1, U13.21 (CAP)
unnamed: C24.1, R72.1, U13.1 (VDDIO), U13.3 (VDDIO), U13.22 (VDD), U13.23 (VDD)
unnamed: C26.1, R73.1, U12.2 (VCC)
unnamed: C27.1, R74.1, U14.1 (VDDIO), U14.14 (VDD), U14.15 (VDDR)
unnamed: C28.1, R75.1, U15.2 (CSB), U15.6 (VDDIO), U15.8 (VDD)
unnamed: C29.1, R76.1, U16.6 (VDD)
unnamed: J6.1, Q26.3 (D)
unnamed: J7.1, R80.1
unnamed: Q26.1 (G), R77.2, R78.1
unnamed: Q27.3 (D), R78.2
SENSORS_CS_AG: U13.7 (CS_A/G); also elsewhere on the board
SENSORS_CS_LIS: U14.8 (CS); also elsewhere on the board
SENSORS_CS_M: U13.8 (CS_M); also elsewhere on the board
SENSORS_MISO: U13.5 (SDO_A/G), U13.6 (SDO_M), U14.7 (MISO); also elsewhere on the board
SENSORS_MOSI: U13.4 (SDA/SDI/SDO), U14.6 (MOSI); also elsewhere on the board
SENSORS_RX: J7.3; also elsewhere on the board
SENSORS_SCL: U12.6 (SCL), U15.4 (SCK), U16.10 (SCL); also elsewhere on the board
SENSORS_SCLK: U13.2 (SCL/SPC), U14.4 (SCL); also elsewhere on the board
SENSORS_SDA: U12.5 (SDA), U15.3 (SDI), U16.9 (SDA); also elsewhere on the board
SENSORS_TX: J7.2; also elsewhere on the board

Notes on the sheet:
I2C Address: 0x5A
Do Not Place Resistor
I2C Address: 0x28
Accelerometer/ Magnetometer/ Gyro
Temperature/ Pressure/ Humidity
I2C Address: 0x76
Air Quality
Balloon Network Pressure
Stratologger Altimeter

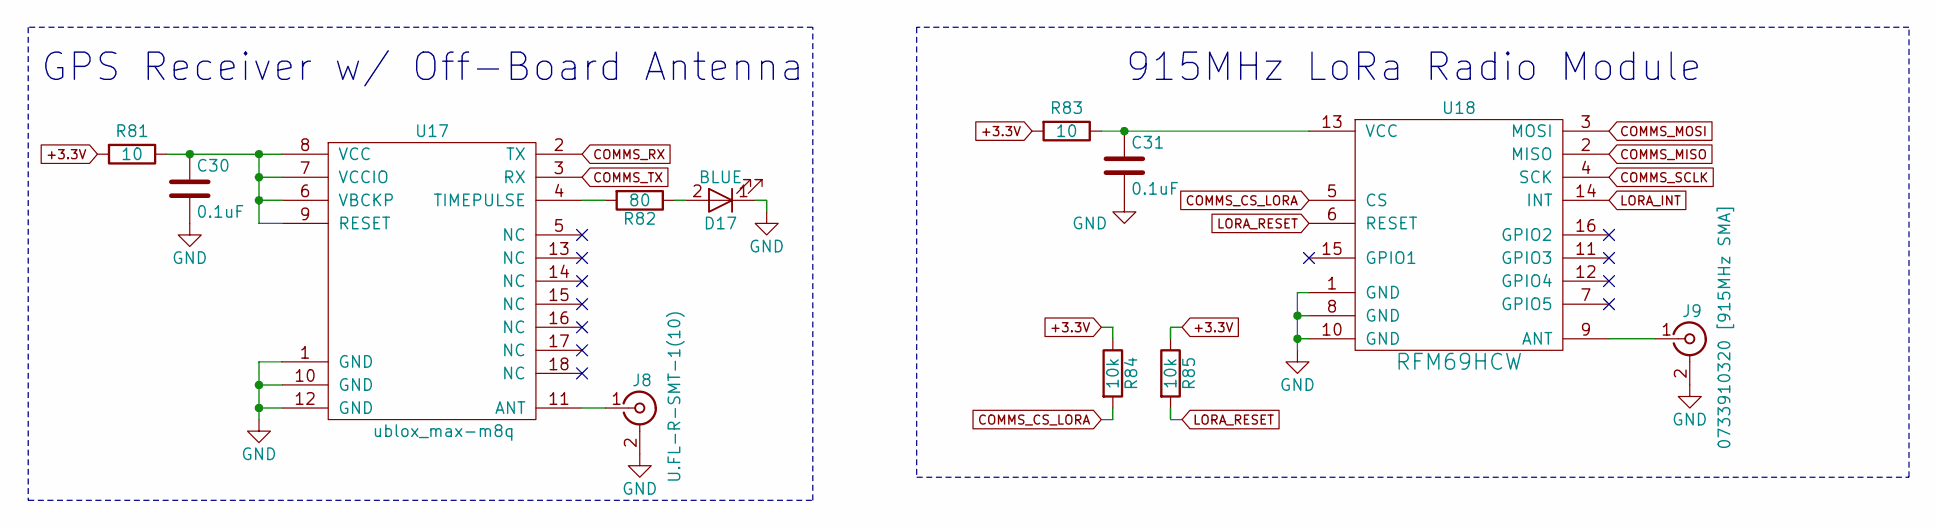
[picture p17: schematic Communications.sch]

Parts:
C30, C31: 0.1uF; C_0603_HandSoldering
D17: BLUE; LED_0603_HandSoldering
J8: U.FL-R-SMT-1(10); HRS_U.FL-R-SMT-1(10)
J9: 0733910320 [915MHz SMA]; CONN_RP-SMA_Right_Angle_0733910320
R81, R83: 10; R_0603_HandSoldering
R82: 80; R_0603_HandSoldering
R84, R85: 10k; R_0603_HandSoldering
U17: ublox_max-m8q; MAX-M8
U18: RFM69HCW; RFM69HCW-XXXS2

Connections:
+3.3V: R81.2, R83.2, R84.1, R85.1; also elsewhere on the board
COMMS_CS_LORA: R84.2, U18.5 (CS); also elsewhere on the board
COMMS_MISO: U18.2 (MISO); also elsewhere on the board
COMMS_MOSI: U18.3 (MOSI); also elsewhere on the board
COMMS_RX: U17.2 (TX); also elsewhere on the board
COMMS_SCLK: U18.4 (SCK); also elsewhere on the board
COMMS_TX: U17.3 (RX); also elsewhere on the board
GND: C30.2, C31.2, D17.1 (K), J8.2 (Ext), J9.2 (Ext), U17.1 (GND), U17.10 (GND), U17.12 (GND), U18.1 (GND), U18.8 (GND), U18.10 (GND); also elsewhere on the board
LORA_INT: U18.14 (INT); also elsewhere on the board
LORA_RESET: R85.2, U18.6 (RESET); also elsewhere on the board
unnamed: C30.1, R81.1, U17.6 (VBCKP), U17.7 (VCCIO), U17.8 (VCC), U17.9 (RESET)
unnamed: C31.1, R83.1, U18.13 (VCC)
unnamed: D17.2 (A), R82.1
unnamed: J8.1 (In), U17.11 (ANT)
unnamed: J9.1 (In), U18.9 (ANT)
unnamed: R82.2, U17.4 (TIMEPULSE)

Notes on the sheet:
GPS Receiver w/ Off-Board Antenna
915MHz LoRa Radio Module

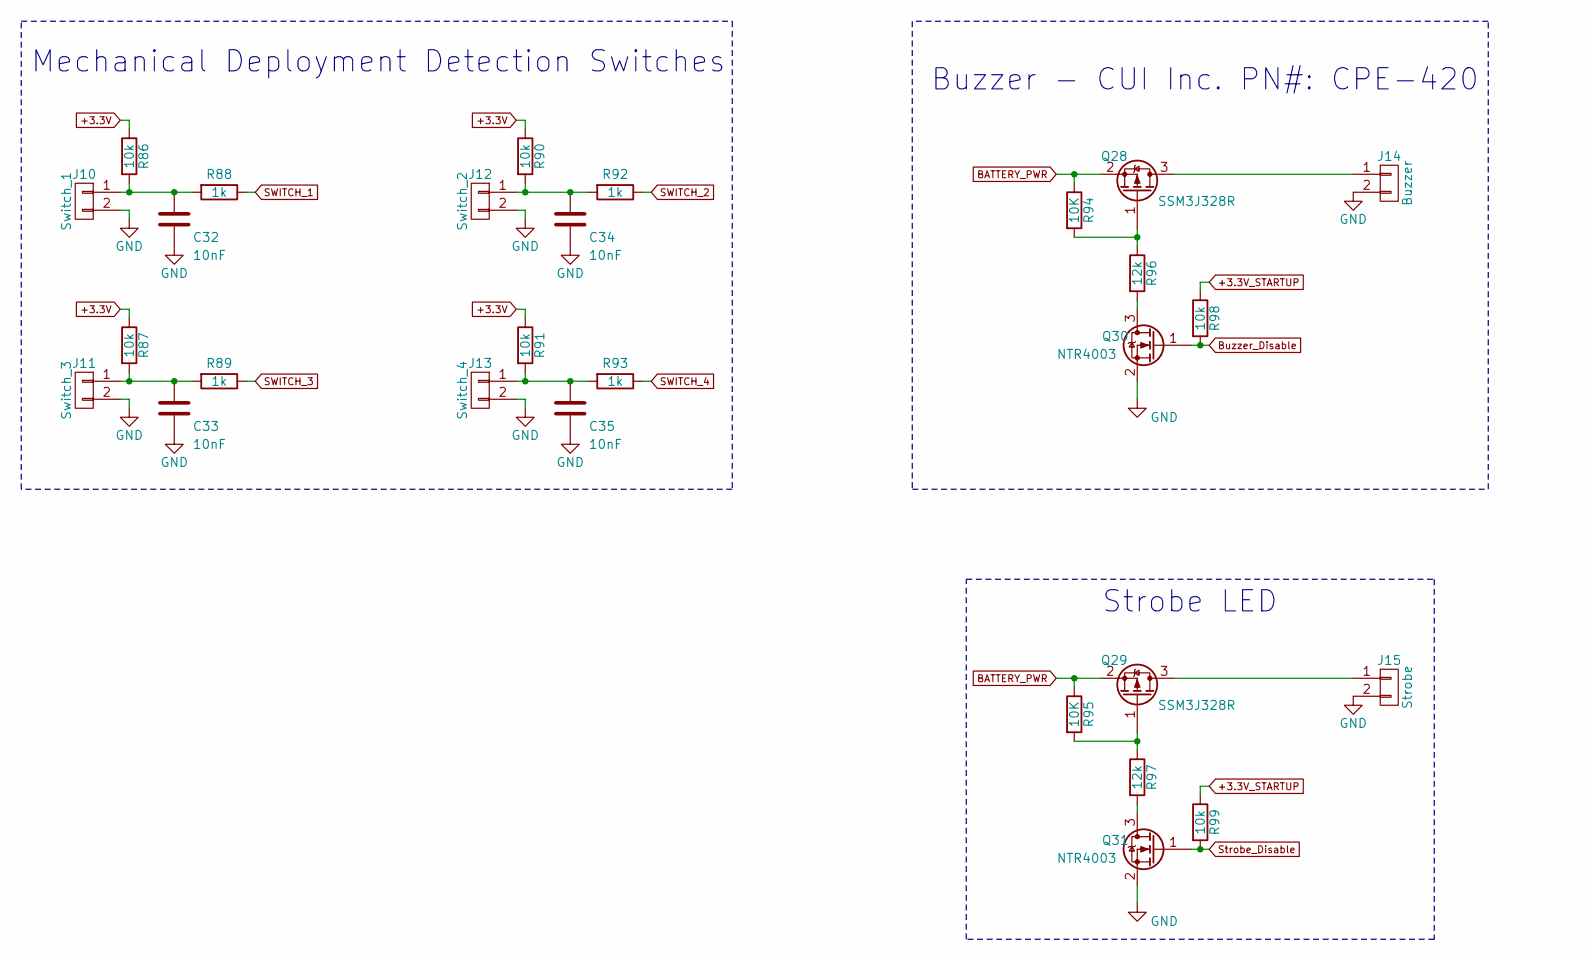
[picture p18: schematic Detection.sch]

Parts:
C32, C33, C34, C35: 10nF; C_0603_HandSoldering
J10: Switch_1; CONN_2POS_VERT_TE_CONN_LOCK_5-103669-1
J11: Switch_3; CONN_2POS_VERT_TE_CONN_LOCK_5-103669-1
J12: Switch_2; CONN_2POS_VERT_TE_CONN_LOCK_5-103669-1
J13: Switch_4; CONN_2POS_VERT_TE_CONN_LOCK_5-103669-1
J14: Buzzer; CONN_2POS_VERT_TE_CONN_LOCK_5-103669-1
J15: Strobe; CONN_2POS_VERT_TE_CONN_LOCK_5-103669-1
Q28, Q29: SSM3J328R; SOT-23
Q30, Q31: NTR4003; SOT-23
R86, R87, R90, R91, R98, R99: 10k; R_0603_HandSoldering
R88, R89, R92, R93: 1k; R_0603_HandSoldering
R94, R95: 10K; R_0603_HandSoldering
R96, R97: 12k; R_0603_HandSoldering

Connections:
+3.3V: R86.1, R87.1, R90.1, R91.1; also elsewhere on the board
+3.3V_STARTUP: R98.1, R99.1; also elsewhere on the board
BATTERY_PWR: Q28.2 (S), Q29.2 (S), R94.1, R95.1; also elsewhere on the board
Buzzer_Disable: Q30.1 (G), R98.2; also elsewhere on the board
GND: C32.2, C33.2, C34.2, C35.2, J10.2, J11.2, J12.2, J13.2, J14.2, J15.2, Q30.2 (S), Q31.2 (S); also elsewhere on the board
unnamed: C32.1, J10.1, R86.2, R88.2
unnamed: C33.1, J11.1, R87.2, R89.2
unnamed: C34.1, J12.1, R90.2, R92.2
unnamed: C35.1, J13.1, R91.2, R93.2
unnamed: J14.1, Q28.3 (D)
unnamed: J15.1, Q29.3 (D)
unnamed: Q28.1 (G), R94.2, R96.1
unnamed: Q29.1 (G), R95.2, R97.1
unnamed: Q30.3 (D), R96.2
unnamed: Q31.3 (D), R97.2
SWITCH_1: R88.1; also elsewhere on the board
SWITCH_2: R92.1; also elsewhere on the board
SWITCH_3: R89.1; also elsewhere on the board
SWITCH_4: R93.1; also elsewhere on the board
Strobe_Disable: Q31.1 (G), R99.2; also elsewhere on the board

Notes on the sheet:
Mechanical Deployment Detection Switches
Buzzer - CUI Inc. PN#: CPE-420
Strobe LED

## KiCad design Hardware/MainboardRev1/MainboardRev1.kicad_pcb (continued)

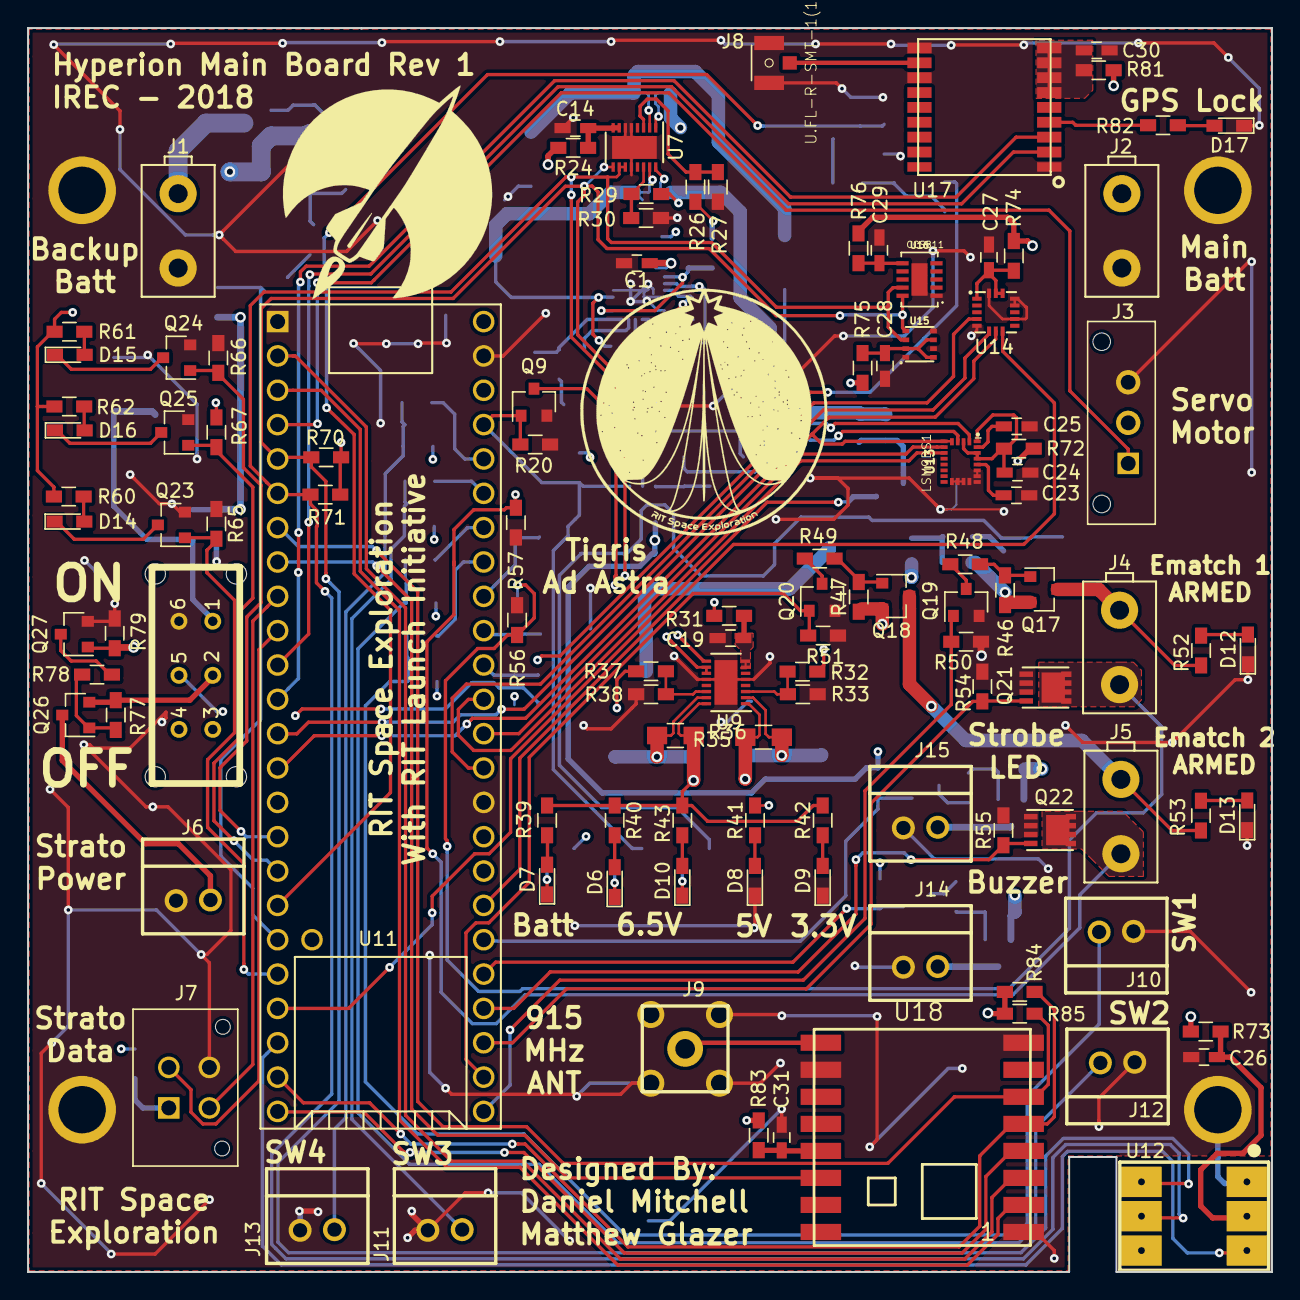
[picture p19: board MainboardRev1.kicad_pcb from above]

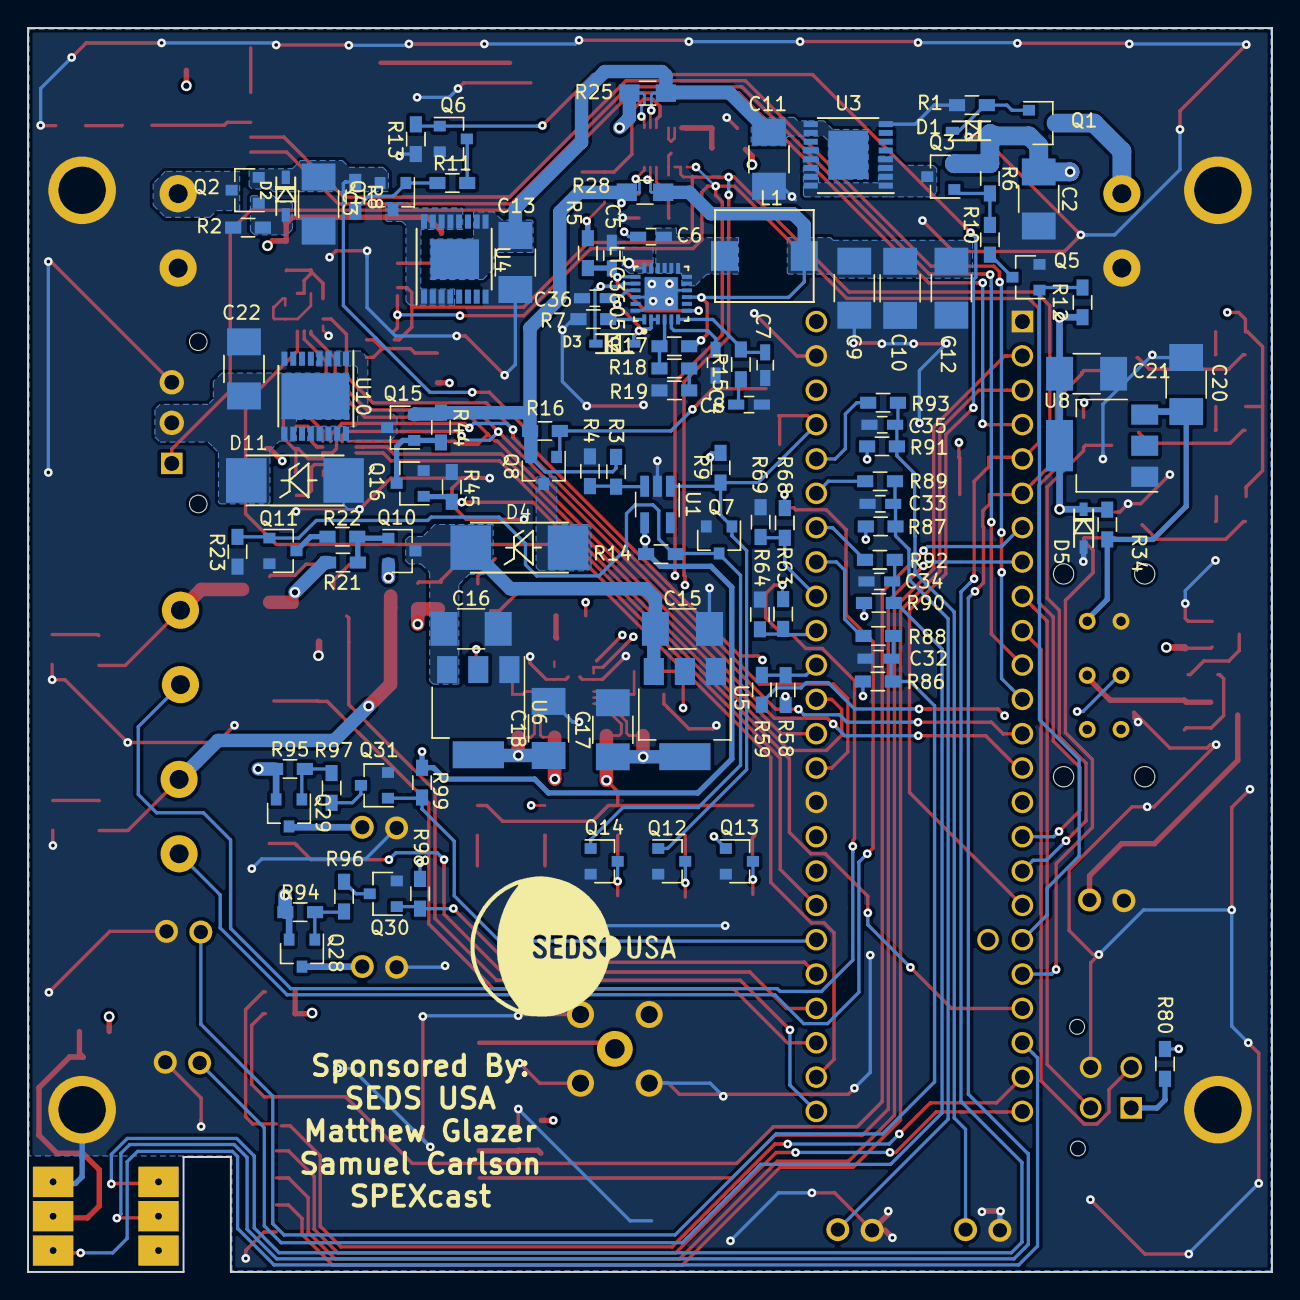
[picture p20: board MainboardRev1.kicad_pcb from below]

Board: 4 copper layers, 92.0 x 92.0 mm, 222 parts (106 on the bottom side), 141 nets.

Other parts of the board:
C36: C_0603_HandSoldering

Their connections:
GND: C36.1; also elsewhere on the board
unnamed 67: C36.2; also elsewhere on the board

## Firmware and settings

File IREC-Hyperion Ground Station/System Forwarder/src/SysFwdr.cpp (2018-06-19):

/**
 * Hyperion - IREC
 * File: SysFwdr.cpp
 * Organization: RIT Space Exploration
 * Desc
 *    	Main program used to forward packets from LoRa Module to 
 *		desktop
 */

#include <SPI.h>
#include <IREC_Hyperion_Protocol.h>
#include <RH_RF95.h>

#define BAUD_RATE 115200
#define INITAL_STR_SIZE 200
#define MAX_MSG_LEN_RECV 100

// SPI pins
#define RFM95_RST     6   // "A"
#define RFM95_CS      5   // "B"
#define RFM95_INT     4    // "C"

#define RF95_FREQ 915.0

RH_RF95 rf95(RFM95_CS, RFM95_INT);
bool armed = false;
bool sent_cmd = false;

/**
 * Convert int32_t into a float
 */
float convert_int32_float(int32_t inputvalue) {
	float f;
	memcpy(&f, &inputvalue, sizeof(f));
	return f;
}

/**
 * Convert float into a int32_t
 */
int32_t convert_float_int32(float inputvalue) {
	int32_t f;
	memcpy(&f, &inputvalue, sizeof(f));
	return f;
}

/**
 * Create the header section of the data string to be sent over
 * a Serial connection.
 * Args:
 * 		buff: the source string
 * 		hdr: the header struct
 * Format:
 * 		[DataType],[F1],[F2],[F3],[F4],[Time]
 * Return:
 * 		The length of the compiled string
 */
int write_header(char* buff, unpk_header hdr){

	char temp[10] = {'\0'};
	
	itoa(hdr.data_type, temp, 10);
	strcat(buff, temp);

	for(int i = 0; i < 4; i++){
		strcat(buff, ",");
		if((hdr.flags >> 3-i) & 1){
			strcat(buff, "1");
		} else {
			strcat(buff, "0");
		}
	}

	strcat(buff, ",");
	itoa(hdr.time, temp, 10);
	strcat(buff, temp);

	return strlen(buff);
}

/**
 * Individual csv converter from LSM9DS1 packet to data string
 * Args:
 * 		buff: the source string
 * 		data: raw data struct
 * Format:
 * 		[Header],[ax],...,[gx],...,[mx]
 * Returns:
 * 		The length of the string constructed
 */
int CtCSV_LSM9DS1(char* buff, LSM9DS1_Packet data){
	
	LSM9DS1_Data data_frame = data.data;

	write_header(buff, data.header);

	int32_t temp_arry[9] = {data_frame.ax, data_frame.ay, data_frame.az,
							data_frame.gx, data_frame.gy, data_frame.gz,
							data_frame.mx, data_frame.my, data_frame.mz};
	
	char temp[10] = {'\0'};

	for(int i = 0; i < 9; i++){
		strcat(buff, ",");
		float res = convert_int32_float(temp_arry[i]);
		dtostrf(res, 1, 3, temp);
		strcat(buff, temp);
	}

	return strlen(buff);
}

/**
 * Construct a string to be sent over serial for the BME280
 * Args:
 * 		buff: the string to be constructed
 * 		data: raw data structure
 * Format:
 * 		[Header],[temp],[press],[hum],[alt]
 * Return:
 * 		The size of the constructed string
 */
int CtCSV_BME280(char* buff, BME280_Packet data){

	BME280_Data data_frame = data.data;

	write_header(buff, data.header);

	int32_t temp_arry[4] = {data_frame.temperature, data_frame.pressure,
							data_frame.humidity, data_frame.altitude};
	
	char temp[10] = {'\0'};

	for(int i = 0; i < 4; i++){
		strcat(buff, ",");
		float res = convert_int32_float(temp_arry[i]);
		dtostrf(res, 1, 3, temp);
		strcat(buff, temp);
	}

	return strlen(buff);
}

/**
 * Construct a string to be sent over serial for the CCS811 data frame
 * Args:
 * 		buff: the string to be constructed
 * 		data: raw data structure
 * Format:
 * 		[Header],[Co2],[TVOC]
 * Return:
 * 		The size of the constructed string.
 */
int CtCSV_CCS811(char* buff, CCS811_Packet data){

	CCS811_Data data_frame = data.data;

	write_header(buff, data.header);

	int16_t temp_arry[2] = {data_frame.co2, data_frame.TVOC};
	
	char temp[10] = {'\0'};

	for(int i = 0; i < 2; i++){
		strcat(buff, ",");
		itoa(temp_arry[i], temp, 10);
		strcat(buff, temp);
	}

	return strlen(buff);
}

/**
 * Individual csv converter from LIS331 packet to data string
 * Args:
 * 		buff: the source string
 * 		data: raw data struct
 * Format:
 * 		[Header],[ax]
 * Returns:
 * 		The length of the string constructed
 */
int CtCSV_LIS331(char* buff, LIS311_Packet data){
	LIS311_Data data_frame = data.data;

	write_header(buff, data.header);

	int32_t temp_arry[3] = {data_frame.ax, data_frame.ay, data_frame.az};
	
	char temp[10] = {'\0'};

	for(int i = 0; i < 3; i++){
		strcat(buff, ",");
		float res = convert_int32_float(temp_arry[i]);
		dtostrf(res, 1, 3, temp);
		strcat(buff, temp);
	}

	return strlen(buff);
}

/**
 * Construct a csv string for data in a PFSL data frame
 * Args:
 * 		buff: the source string
 * 		data: raw data struct
 * Format:
 * 		[Header],[alt]
 * Returns:
 * 		The length of the string constructed
 */
int CtCSV_PFSL(char* buff, PFSL_Packet data){
	PFSL_Data data_frame = data.data;

	write_header(buff, data.header);

	char temp[10] = {'\0'};

	strcat(buff, ",");
	float res = convert_int32_float(data_frame.alt);
	dtostrf(res, 1, 3, temp);
	strcat(buff, temp);

	return strlen(buff);
}

/**
 * Construct a csv string using the unpacked orientation data
 * Args:
 * 		buff: the source string
 * 		data: raw data struct
 * Format:
 * 		[Header],[Pitch],[Roll],[Yaw]
 * Returns:
 * 		The length of the string constructed
 */
int CtCSV_Oren(char* buff, OREN_Packet data){
	OREN_Data data_frame = data.data;

	write_header(buff, data.header);

	char temp[10] = {'\0'};

	int16_t temp_arry[3] = {data_frame.pitch, data_frame.roll, data_frame.yaw};

	for(int i = 0; i < 3; i++){
		strcat(buff, ",");
		itoa(temp_arry[i], temp, 10);
		strcat(buff, temp);
	}

	return strlen(buff);
}

/**
 * Construct a csv string from data within a raw struct.
 * Args:
 * 		buff: the source string
 * 		data: raw data struct
 * Format:
 * 		[Header],[String]
 * Returns:
 * 		The length of the string constructed
 */
int CtCSV_Info(char* buff, Info_Packet data){

	write_header(buff, data.header);
	strcat(buff, ",");
	strcat(buff, data.data);

	return strlen(buff) + 1;
}

/**
 * Send command to ground station with current status
 */
void send_command(){

	rf95.waitPacketSent();

	uint16_t time = millis() / 1000;
	uint8_t buff[HEADER_SIZE] = {0};

	if(armed){
		char flags[4] = {1, 0, 0, 0};
		IRECHYPERP::createCMMNDFrame(buff, flags, time);
	} else {
		char flags[4] = {0, 1, 0, 0};
		IRECHYPERP::createCMMNDFrame(buff, flags, time);      
	}

	rf95.send(buff, HEADER_SIZE);
}

/**
 * Grabs source from transmission, unpacks data then 
 * converts packed data a comma seperated string.
 * CSV format: 
 * [type],[flag1(1,0)],[flag2(1,0)],[flag3(1,0)],[flag4(1,0)],[time(seconds)],[data],[data]...
 * Arguments
 * 		buff, the buffer which the csv string will be placed.
 * 		source, the raw bytes from the payload.
 * Return
 * 		The number of bytes within the buff
 */
int convert_to_csv(char* buff, const uint8_t* source){

	switch(IRECHYPERP::typeofData(source)){
		case NULLDATAt:
		{
			//No data
		}
		break;
		case LSM9DS1t:
		{
			LSM9DS1_Packet packet = IRECHYPERP::unpack_LSM9DS1(source);
			CtCSV_LSM9DS1(buff, packet);
		}
		break;
		case BME280t:
		{
			BME280_Packet packet = IRECHYPERP::unpack_BME280(source);
			CtCSV_BME280(buff, packet);
		}
		break;
		case CCS811t:
		{
			CCS811_Packet packet = IRECHYPERP::unpack_CCS811(source);
			CtCSV_CCS811(buff, packet);
		}
		break;
		case LIS331t:
		{
			LIS311_Packet packet = IRECHYPERP::unpack_LIS311(source);
			CtCSV_LIS331(buff, packet);
		}
		break;
		case PFSLt:
		{
			PFSL_Packet packet = IRECHYPERP::unpack_PFSL(source);
			CtCSV_PFSL(buff, packet);
		}
		break;
		case Orent:
		{
			OREN_Packet packet = IRECHYPERP::unpack_Oren(source);
			CtCSV_Oren(buff, packet);
		}
		break;
		case CMMNDt:
		{
			CMMND_Packet packet = IRECHYPERP::unpack_CMMND(source);

			if(packet.header.flags & 1){
				strcat(buff, "8,0,0,0,0,0,PAYLOAD IS !DISARMED!");
			}
			if((packet.header.flags >> 1) & 1){
				strcat(buff, "8,0,0,0,0,0,PAYLOAD IS !ARMED!");
			}

			if(sent_cmd){
				send_command();
				sent_cmd = false;
			}
		}
		break;
		case INFOt:
		{
			Info_Packet packet = IRECHYPERP::unpack_Info(source);
			CtCSV_Info(buff, packet);
		}
		break;
	}
}

/**
 * Recieve incomming messages then handle them according
 * to which data type they contain.
 */
void handle_incomming_messages(){

	if (rf95.available()){ 

		digitalWrite(LED_BUILTIN, HIGH);

    	uint8_t buff_raw_msg[MAX_MSG_LEN_RECV];
		char buff_strng[INITAL_STR_SIZE] = {'\0'};

		uint8_t len = sizeof(buff_raw_msg);

    	if (rf95.recv(buff_raw_msg, &len)){
			convert_to_csv(buff_strng, buff_raw_msg);
			Serial.println(buff_strng);
    	}
		digitalWrite(LED_BUILTIN, LOW);
  	}
}

/**
 * Init function for the lora.
 */
int init_LoRa(){

  pinMode(RFM95_RST, OUTPUT);
  digitalWrite(RFM95_RST, HIGH);
  
  // manual reset
  digitalWrite(RFM95_RST, LOW);
  delay(10);
  digitalWrite(RFM95_RST, HIGH);
  delay(10);

  if (!rf95.init()) {
	  return 1;
  }

  // Defaults after init are 434.0MHz, modulation GFSK_Rb250Fd250, +13dbM
  if (!rf95.setFrequency(RF95_FREQ)) {
	  return 1;
  }

  // maximum power
  rf95.setTxPower(23, false);

  return 0;
}

/**
 * Main initialize function for the SysFwdr program.
 */
void init_sys(){
	// Place startup code here
	Serial.begin(BAUD_RATE);
	// Pin mode for led
	pinMode(LED_BUILTIN, OUTPUT);
	digitalWrite(LED_BUILTIN, LOW);

	init_LoRa();
}

/**
 * Function used to simulate orientation data
 */
void simulate_oren(){
	static int32_t pitch = 0;
	static int32_t roll = 0;
	static int32_t yaw = 0;

	pitch = (pitch < 180) ? ++pitch : -180;
	roll = (roll < 180) ? ++roll : -180;
	yaw = (yaw < 180) ? ++yaw : -180;

	uint8_t buff[300] = {0};
	char flags[4] = {0, 0, 0, 0};

	IRECHYPERP::createOrenFrame(buff, flags, (uint16_t) (millis()/100),
								pitch, roll, yaw);

	OREN_Packet packet = IRECHYPERP::unpack_Oren(buff);

	char strbuff[300] = {'\0'};

	CtCSV_Oren(strbuff, packet);

	Serial.println(strbuff);
}

void simulate_alt(){
	static int32_t alto = 0;
	static bool falling = false;

	if(alto > 10000) falling = true;
	if(alto < 100) falling = false;

	if(falling) alto -= 2;
	else alto += 2;

	uint8_t buff[300] = {0};
	char flags[4] = {0, 0, 0, 0};

	IRECHYPERP::createPFSLFrame(buff, flags, (uint16_t) (millis()/100), alto);

	PFSL_Packet packet = IRECHYPERP::unpack_PFSL(buff);

	char strbuff[300] = {'\0'};

	CtCSV_PFSL(strbuff, packet);

	Serial.println(strbuff);
}

void simulate_LIS331(){
	float ay = rand()%RAND_MAX;
	float ax = rand()%RAND_MAX;
	float az = rand()%RAND_MAX;

	uint8_t buff[300] = {0};
	char flags[4] = {0, 0, 0, 0};

	IRECHYPERP::createLIS311Frame(buff, flags, (uint16_t) (millis()/100),
	convert_float_int32(ax), convert_float_int32(ay), convert_float_int32(az));

	LIS311_Packet packet = IRECHYPERP::unpack_LIS311(buff);

	char strbuff[300] = {'\0'};

	CtCSV_LIS331(strbuff, packet);

	Serial.println(strbuff);
}

void simulate_BME280(){
	float alt = rand();
	float pressure = rand() % 100;
	float temp = rand() % 150;
	float hum = rand() % 100;

	uint8_t buff[300] = {0};
	char flags[4] = {0, 0, 0, 0};

	IRECHYPERP::createBME280Frame(buff, flags, (uint16_t) (millis()/100),
	convert_float_int32(temp), convert_float_int32(hum), convert_float_int32(pressure), convert_float_int32(alt));

	BME280_Packet packet = IRECHYPERP::unpack_BME280(buff);

	char strbuff[300] = {'\0'};

	CtCSV_BME280(strbuff, packet);

	Serial.println(strbuff);
}

void sim(){
	simulate_oren();
	simulate_alt();
	simulate_LIS331();
	simulate_BME280();

	delay(17);
}

/**
 * Check user input for command updates
 */
void check_inpt(){

	String usr;

	if(Serial.available()){
		usr = Serial.readString();

		if(usr.equals("ARM")){
			armed = true;
			sent_cmd = true;
			Serial.println("8,0,0,0,0,0,Arming Payload!");
		}
		if(usr.equals("DISARM")){
			armed = false;
			sent_cmd = true;
			Serial.println("8,0,0,0,0,0,Disarming Payload!");
		}
	}
}

int main(){

	init_sys();

	while(true){

		check_inpt();
		handle_incomming_messages();
	}
}

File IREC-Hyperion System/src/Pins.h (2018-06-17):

/*
 * Hyperion - IREC
 * File: Pins.h
 * Organization: RIT Space Exploration
 * Description
 *    Header file used to define pins with corresponding macros.
 */

#ifndef PINS_H
#define PINS_H

// PCB Pins

#define COMMS_MOSI      0
#define COMMS_MISO      1
#define SERVO_PWM       2
#define SENSORS_SCL     3
#define SENSORS_SDA     4
#define LORA_RST        5
#define LORA_INT        6
#define SENSORS_RX      7
#define SENSORS_TX      8
#define COMMS_RX        9
#define COMMS_TX        10
#define SENSORS_MOSI    11
#define SESNORS_MISO    12
#define SENSORS_SCLK    13
#define SENSORS_CS_AG   14
#define SENSORS_CS_M    15
#define MAIN_BATT_ANLG  16
#define EMATCH_1_ANLG   17
#define EMATCH_2_ANLG   18
#define SWITCH_01       19
#define SWITCH_02       20
#define SWITCH_03       21
#define SWITCH_04       22
#define CONTROL_1       23
#define LED_BLUE        24
#define LED_RED         25
#define MAIN_BATT_EN    26
#define BACKUP_BATT_EN  27
#define LED_GREEN       28
#define SERVO_PWR_EN    29
#define INT_PRESSURE    30
#define COMMS_CS_LORA   31
#define COMMS_SCLK      32
#define EMATCH_1_ARM    33
#define EMATCH_2_ARM    34
#define EMATCH_1_FIRE   35
#define EMATCH_2_FIRE   36
#define BUZZER_DISABLE  37
#define STROBE_DISABLE  38
#define SENSOR_CS_LIS   39

// PROTO_PINS
/**
#define RFM95_INT       4  
#define RFM95_CS        5 
#define RFM95_RST       6
#define LSM9DS1_M_CS    10 
#define LIS3DH_MOSI     11
#define LIS3DH_MISO     12
#define LIS3DH_CLK      13
#define HEARTBEAT_LED   22
#define LSM9DS1_AG_CS   24
#define DEPLOY_SWITCH_01 25 
#define DEPLOY_SWITCH_02 26 
#define DEPLOY_SWITCH_03 27 
#define DEPLOY_SWITCH_04 28 
#define EMATCH_1_ARM_P    23
#define EMATCH_1_FIRE_P   21
#define LIS3DH_CS        35
*/

#endif
 

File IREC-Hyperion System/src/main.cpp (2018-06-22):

/*
 * main.cpp
 * Organization: RIT Space Exploration
 * Desc:
 *    Main entry point into the Hyperion system.
 */

#include "IRECHYPERION.h"
#include <Arduino.h>
#include "sensorUtils/LSM9DS1_Hyperion.h"
#include "sensorUtils/BME280_Hyperion.h"
#include "sensorUtils/CCS811_Hyperion.h"
#include "sensorUtils/GPS_Hyperion.h"
#include "sensorUtils/LIS331_Hyperion.h"
#include "sensorUtils/StratoLogger_Hyperion.h"
#include "generalUtils/Mission_Utils_Hyperion.h"
#include "generalUtils/Health_Check_Hyperion.h"
#include "Routines_Hyperion.h"
#include "Transmit_Hyperion.h"
#include "Data_Buffer_Hyperion.h"

#define DSQ_MAIN_CAP 100
#define BATT_SWITCH 9.9

// Current DSQ in use
DSQ dsq(DSQ_MAIN_CAP);// Dynamic Scheduling Queue (DSQ)

/**
 * add startup routines to the dsq for main phase
 */
void fill_main_startup(){
	//TODO
	// Add startup routines into the dsq
	//dsq.add_routine(0, 3, R_trans_LSM9DS1);
	dsq.add_routine(0, 20, R_trans_BME280);
	//dsq.add_routine(0, 30, R_trans_CCS811);
	//dsq.add_routine(0, 10, R_trans_LIS331);
	dsq.add_routine(0, 10, R_trans_Altitude);
	//dsq.add_routine(0, 10, R_trans_Orientation);
	dsq.add_routine(0, 100, R_trans_GPS);
	dsq.add_routine(0, 3, R_seq_LSM9DS1_data);
	dsq.add_routine(0, 20, R_seq_BME280_data);
	//dsq.add_routine(0, 30, R_seq_CCS811_data);
	//dsq.add_routine(0, 3, R_seq_LIS331_data);
	dsq.add_routine(0, 100, R_calc_RateOfClimb);
	dsq.add_routine(0, 10, R_Altitude_data);
	dsq.add_routine(0, 10, R_seq_Altitude_data);
	dsq.add_routine(0, 1, R_check_deployment);
	dsq.add_routine(0, 3, R_gath_LSM9DS1_data);
	dsq.add_routine(0, 20, R_gath_BME280_data);
	dsq.add_routine(0, 10, R_gath_GPS_data);
	//dsq.add_routine(0, 3, R_gath_LIS331_data);
	dsq.add_routine(0, 50, R_recv_Disarm);
	dsq.add_routine(0, 100, R_Heartbeat);
	dsq.add_routine(0, 50, R_Strobe);
}

/**
 * add startup routines to the dsq for suspended phase
 */
void fill_safe_startup(){
	
	dsq.add_routine(0, 100, R_calc_RateOfClimb);
	dsq.add_routine(0, 10, R_Altitude_data);
	dsq.add_routine(0, 3, R_gath_LSM9DS1_data);
	dsq.add_routine(0, 20, R_gath_BME280_data);
	dsq.add_routine(0, 10, R_gath_GPS_data);
	//dsq.add_routine(0, 3, R_gath_LIS331_data);
	dsq.add_routine(0, 3, R_trans_LSM9DS1);
	dsq.add_routine(0, 20, R_trans_BME280);
	dsq.add_routine(0, 100, R_trans_GPS);
	//dsq.add_routine(0, 30, R_trans_CCS811);
	//dsq.add_routine(0, 10, R_trans_LIS331);
	dsq.add_routine(0, 10, R_trans_Altitude);
	//dsq.add_routine(0, 10, R_trans_Orientation);
	dsq.add_routine(0, 50, R_recv_Arm);
	dsq.add_routine(0, 100, R_Heartbeat);
	dsq.add_routine(0, 200, R_Health_report);
}

/**
 * add startup routines to the dsq for done phase
 */
void fill_done_startup(){
	
	dsq.add_routine(0, 100, R_Heartbeat);
	dsq.add_routine(0, 50, R_Strobe);
	dsq.add_routine(0, 1, R_Delay);
	dsq.add_routine(0, 10, R_gath_GPS_data);
	dsq.add_routine(0, 100, R_trans_GPS);
}

/**
 * Switches to the main flight phase, ARMED
 */
void switch_to_main(){

	dsq.clear();
	fill_main_startup();
}

/**
 * Switches to done phase after mission success
 */
void switch_to_done(){

	dsq.clear();
	fill_done_startup();
}

/**
 * Switches to safe phase on command
 */
void switch_to_safe(){

	digitalWriteFast(BUZZER_DISABLE, LOW); // Disable Buzzer
	digitalWriteFast(STROBE_DISABLE, LOW); // Disable Strobe

	dsq.clear();
	fill_safe_startup();
}

/**
 * Routine sets modes of pin(s):
 * 		LED_BLUE, LED_GREEN, LED_RED
 */
void init_misc_pins(){
	// Init Heartbeat led
	pinMode(LED_BLUE, OUTPUT);
	digitalWriteFast(LED_BLUE, LOW);

	// Init SD IO led
	pinMode(LED_GREEN, OUTPUT);
	digitalWriteFast(LED_GREEN, LOW);

	pinMode(LED_RED, OUTPUT);
	digitalWriteFast(LED_RED, LOW);

	// Init for strobe led
	pinMode(STROBE_DISABLE, OUTPUT);
	digitalWriteFast(STROBE_DISABLE, LOW);

	// Init for buzzer
	pinMode(BUZZER_DISABLE, OUTPUT);
	digitalWriteFast(BUZZER_DISABLE, LOW);

	pinMode(MAIN_BATT_EN, OUTPUT);
	digitalWriteFast(MAIN_BATT_EN, LOW);
}

/**
 * Checks health of power system, adjusts power source accordantly.
 */
void power_system_check(){
	
	float mainBattVolt = analogRead(MAIN_BATT_ANLG);
	mainBattVolt *= (3.3 / 1023.0);
	mainBattVolt /= 0.23866;

	if(mainBattVolt > BATT_SWITCH){ // Main battery ok
		digitalWriteFast(MAIN_BATT_EN, HIGH);
	} else {
		digitalWriteFast(LED_RED, HIGH);
		digitalWriteFast(MAIN_BATT_EN, LOW);
		send_report("MAIN BATTERY IS BELOW VOLTAGE THRESHOLD!\0");
	}
}

void setup() {
	delay(4000);
	analogReadAveraging(16); // Smooths out analog readings

	// TODO
	// Initialize hardware modules
	init_misc_pins();
	init_para_pins();
	init_LoRa();
	init_BME280();
	init_LSM9DS1();
	//init_CCS811();
	init_gps();
	init_LIS331();
	init_StratoLogger();
	init_SD();
	init_deploy_pins(); // Initialize pins which deployment switches are attached.
	power_system_check();

	// Add Default routine to the dsq
	dsq.set_default(1, R_Default);

	fill_safe_startup();
}

/**
 * Main Arduino loop function, calls execution system call
 */
void loop() {
	// Execute routine placed into the DSQ
	dsq.execute();
}

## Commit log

2018-01-29 Flushed out some sensor functions
2018-01-29 Updated Readme with sensor info
2018-01-31 Reworked getter functions in LSM9DS1
    [IRECHYPERION_LSM9DS1.ino]
2018-02-04 added file for reading from the CCS811 gas sensor (assisted by BME280)
2018-02-25 Added Hardware Folder and Initialized Mainboard Project
    [MainboardRev1.kicad_pcb, MainboardRev1.sch]
2018-03-12 Added function prototypes and files to the Hyperion System
2018-03-22 Added some more circuitry to power schematic
    [MainboardRev1.sch]
2018-03-23 Updated CCS811 file with utility functions. Added a utility function file for the LIS331 Sensor.
2018-03-23 Updated function prototypes
2018-03-31 Updated read triggers on the deployment switches from LOW to HIGH. Added thoughts on R_mission_constraints routine
2018-03-31 Changed depoyment error case
2018-03-31 Added utils prototypes for the LIS331
2018-04-03 Fixed init prints
2018-04-03 Removed some print statements
2018-04-04 added some (untested) code for measuring accelerometer data during a drop test
2018-04-06 Added seq and trans routines for the CCS811 sensor. Updated main code to work with phase swaping.
    [main.cpp]
2018-04-09 Worked on Auto Arm code
2018-04-11 Fixed SPI buss hoging issue and added a better Radio-Head Libary
    [LIS331.cpp, Mission_Utils.cpp]
2018-04-13 Removed print
2018-04-18 Fixded spelling and documentation
    [LIS331.cpp, Mission_Utils.cpp]
2018-04-19 Test rx code now accepts more data frames
2018-04-19 Updated transmit code with "fix"
    [LIS331.cpp, LoRa-RFM9x_HyperionProtocol_RX.ino, Mission_Utils.cpp]
2018-04-20 Removed Serial prints
2018-05-14 Schematic Finished. Needs Review & Final Touches. Beginning Footprints...:
    [Actuation.sch, Communications.sch, Controller.sch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]
2018-05-16 Added a pin header file
2018-05-16 Small changes to schematic: Added voltage dividers for analog inputs, small net changes. Added footprints for each part
    [Actuation.sch, Communications.sch, Controller.sch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]
2018-05-16 PCB outline
    [MainboardRev1.kicad_pcb]
2018-05-17 added script for sending data from a ground station to a HABnet instance
2018-05-17 Added arm and disarm routines.
2018-05-17 Components placed. Needs to be routed.
    [Actuation.sch, Communications.sch, Controller.sch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]
2018-05-17 Modified SPI busses, added more error checking to launch detect function.
    [Mission_Utils.cpp, Pins.h, Routines.cpp]
2018-05-17 Added proto-ground station
2018-05-18 Added to silkscreen. Updated schematic pdf
    [MainboardRev1.kicad_pcb]
2018-05-18 Added yaw to system and oren routines
2018-05-19 More silk screen updates
    [MainboardRev1.kicad_pcb]
2018-05-19 Disabled some sensor routines temp
2018-05-19 Altered para pins
2018-05-20 Updated arm routine with changes from proto-payload
2018-05-20 Added software debuff on arm sequence and updated pins to match PCB
2018-05-20 Added led pin logic
2018-05-22 Updated switch debouncing to include precentage thresholds.
2018-05-23 Added buzzer and strobe LED. Created BOM. Reannotated. Added sponsors to silkscreen. Needs to be routed and sent out. Good luck Matt!
    [Actuation.sch, BOM.xlsx, Communications.sch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]
2018-05-23 started routing PCB
    [MainboardRev1.kicad_pcb]
2018-05-23 Added a bunch of random libraries and footprints. What you need should be in there somewhere
2018-05-24 continued work on routing, plenty of work still to be done
    commiting my work for the night
    [MainboardRev1.kicad_pcb]
2018-05-24 Modified Heatbeat routine to maintain set interval.
2018-05-24 morning work, continued routing
    shifted some components slightly for better trace routing, so far so good
    [MainboardRev1.kicad_pcb]
2018-05-24 committing progress, estimating the board is approx 1/3 routed
    [MainboardRev1.kicad_pcb]
2018-05-25 All routing except for the antenna connections is finished
    [MainboardRev1.kicad_pcb]
2018-05-25 Added strobe and delay routines + buzzer enables and disables
    [Routines.cpp, main.cpp]
2018-05-26 Added some ground station code for arming/disarming
2018-05-28 added gerbers and an image of the board
    [MainboardRev1-3V3.Cu.gbr, MainboardRev1-B.Cu.gbr, MainboardRev1-B.Mask.gbr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]
2018-05-28 fixed trace width issues relating to the IMU, routed the antenna traces
    [MainboardRev1.kicad_pcb]
2018-05-29 changed to work with a teensy 3.6
2018-05-29 fixed bugs with sending orientation data
    [SysFwdr.cpp]
2018-05-29 reworked and split into separate files
    [data_type_util.py, habnet_socket.py, socketsender.py]
2018-05-29 added another (shorter) flag for each argument
    [socketsender.py]
2018-05-29 PCB updated per the DFM checks
    via and trace width changes, changed to meet the requirments per the manufacturer's abilities
    [MainboardRev1.kicad_pcb]
2018-05-29 updated gerbers based on PCB changes
    [MainboardRev1-3V3.Cu.gbr, MainboardRev1-B.Cu.gbr, MainboardRev1-B.Mask.gbr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]
2018-06-01 now a subclass of Thread, added functions so it can recieve data
2018-06-01 split functionality into separate threads, added file writting & input command reading
2018-06-07 Sorry alec fixed now
    [SysFwdr.cpp]
2018-06-07 Fixed conversion to string issue
    [SysFwdr.cpp]
2018-06-07 fix some incorrect data keys & convert to values to integers
    [data_type_util.py]
2018-06-08 fixed typo in simulation code
    [SysFwdr.cpp]
2018-06-14 lora init fail msg
    [Transmit.cpp]
2018-06-16 Added check to prevent certain packets of data to get sent to habnet
    [socketsender.py]
2018-06-17 Fixed power routine
2018-06-17 Added TX RX5 fix
    [StratoLogger.cpp, main.cpp]
2018-06-17 Added more logic to arm
2018-06-17 Added more delays to para
2018-06-18 Added print for info
2018-06-19 Print all
2018-06-19 Added print
2018-06-19 Fixed conversion alt error
    [SysFwdr.cpp]
2018-06-19 Updated sea level pressure for NEW MEXICO
2018-07-23 Fixed data
    [BME280_Data.csv, GPS_Data.csv, StratoLogger_Data.csv]
2018-07-25 Added time series plots
    [BME280_Data.csv]
2018-07-27 Fixed naming issue
    [BME280_Data.csv]
